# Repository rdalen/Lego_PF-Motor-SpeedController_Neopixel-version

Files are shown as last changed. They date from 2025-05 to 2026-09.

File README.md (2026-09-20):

# LEGO Power Function (PF) Motor speed controller

A DIY PWM speed controller for LEGO Power Functions motors, featuring a rotary encoder and 16-LED NeoPixel speed/direction indicator.
Inspired by the classic Lego train speed regulator (2868)




<p align="center"><i>2868 Lego train speed regulator</i></p>

---

## Features
- PWM control of LEGO Power Functions motors
- Forward and reverse operation
- Rotary encoder speed control
- 16-LED NeoPixel speed/direction indicator
- Adjustable NeoPixel brightness
- Push-button control
- Long-press reset to stop/default brightness
- Compatible with Arduino Pro Mini and LGT8F328P MiniEVB
- 9 Vdc power input
- Open hardware and software design

---

## Specifications

| Specification  | Value |
| --- | --- |
| Supply voltage | 9Vdc |
| Output voltage | PWM, 0 - 9V |
| Motor driver | DRV8833 |
| MCU | ATmega328P / LGT8F328P |
| NeoPixel ring  | 16 LEDs |
| Rotary encoder | EC11 |
| PCB size | 76 × 100 mm |
| PCB version | v1.1 |
| Motor outputs  | 1 |
| Control | Rotary encoder + push button |

---

## Description
It is based on an Arduino ProMini (or clone) and has a DRV8833 Motor driver module, a Rotary encoder and a 16 LED Neopixel Ring as forward/reverse speed indicator.
The conventional train regulator gives an analog 0-9V output signal. 
In this design, the PF motor is controlled with a Pulse Width Modulation (PWM) output signal. 
This means that the motor speed is controlled by varying the duty cycle of a square wave signal.

Earlier I made [another version](https://github.com/rdalen/Lego_PF-Motor-SpeedController) of a Lego speed controller based on the well known NE555 timer-IC. 

---

## Hardware

- 1× PCB
- 1× MCU Module Arduino Pro Mini or LGT8F328P MiniEVB
- 1× DRV8833 motor driver module
- 1× 16-LED NeoPixel ring
- 1× EC11 rotary encoder with push button
- LEGO PF connectors
- 4-core cable
- 9Vdc power supply / LEGO 8881 battery box
- enclosure material
- 3D-printed knob

Here is the PCB BOM list;



---

### MCU Module

For the MCU modules both the Arduino ProMini and the [LGT8F328P LQFP32 MiniEVB](https://wolles-elektronikkiste.de/en/minievb-boards-an-overview) (Pro Mini Style) can be used or even the [LGT8F328P SSOP20 MiniEVB](https://wolles-elektronikkiste.de/en/minievb-boards-an-overview) (pseudo Pro Mini Style).  

  

You can buy the LGT8F328P MiniEVB modules on AliExpress very cheap.  
I used the 5V version, because not all types of Neopixels are compatible with 3V3.  

---

## The Design
The [design](/docs/Lego%20PF%20Motor%20speed%20controller%20with%20Neopixel%20-%20Schematic.pdf) is made in KiCad 9.0 and is straight forward.  
It can be powered by, for example, a 9V Lego battery box (8881) or by an external 9Vdc power adapter.  
I first tested it in a breadboard setup. 



---

## Build overview

1. Order/assemble the PCB
2. Install the MCU and peripheral modules
3. Modify the PF Cable J11
4. Connect the PF input and motor output
5. Upload the firmware
6. Build the enclosure
7. Install the PCB, encoder and NeoPixel ring
8. Connect the 9Vdc supply
9. Test motor direction and speed indication

---

### The PCB
I designed a 76x100mm PCB, which I ordered from JLCPCB. 



The pcb design takes into account the footprint of the different MCU modules, however **only 1 of the MCU modules needs to be placed**.  

  

PCB v1.0 is shown in the photographs below. It has the issue described in [issue #1](https://github.com/rdalen/Lego_PF-Motor-SpeedController_Neopixel-version/issues/1).  
I still have a few v1.0 boards available for experimenting and sharing. The v1.0 PCB files are also available in the KiCad folder of this repository.

PCB [v1.1](https://github.com/rdalen/Lego_PF-Motor-SpeedController_Neopixel-version/blob/main/src/KiCad9.0/Lego%20PF-Motor%20PWM%20Speedcontroller%20-%20Neopixel%20version-v1.1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) fixes this issue and is the recommended version for new builds.

---

### The DIY PF Cable

On AliExpress you can buy PF connectors and 4 core wire and make your own Lego PF connection cables.
Before assembling the Input PF cable (connected to J11 in the schematic), I removed the C1 and C2 contacts from the Bottom part of the connector so that this connector can be used to connect both the battery box (via the 0V and 9V contacts in the BOTTOM part) as the Lego PF-motor as well (via the C1 and C2 contacts in the TOP part). 

  

The output PF cable (connected to J13 in the schematic) is not modified (so has all its contacts).
So the PF-motor can be connected or to the input connector (connected to the Battery box) or to the output connector.  

See [this article](https://www.philohome.com/pf/pf.htm) about the working of the LEGO Power Function cable.

---

### The Programming

To upload the sketch from your computer into the Arduino board you will need a FTDI USB to TTL Adapter.  



Then;  
- Install the following libraries:
  - [lgt8fx library](https://github.com/dbuezas/lgt8fx?tab=readme-ov-file) (When you use a LGT8F328P MiniEVB Board)
  - [NeoPixel library](https://github.com/adafruit/Adafruit_NeoPixel)
  - [Rotary library](https://github.com/buxtronix/arduino/tree/master/libraries/Rotary)
- Download the sketch (You can also download the sketch from my github)
- Set the proper board settings (see picture below for the LGT8F328P board settings) and upload the sketch



For clarification;
- The NeoPixel ring indicates the output signal (similar to the big yellow button on the conventional LEGO train speed regulator).  
- Turning the Rotary encoder knob to the right will increase the speed in forward direction (Green color), turning to the left will decrease the speed to 0 (LED8 is the center of the indication scale) and then increases the speed in reverse direction (Red color).  
- NeoPixel LED0 is set to blue as power-on indication. 
- When your Rotary encoder is equipped with a push button; a short button press will increase the brightness of the LEDs (in 9 steps) and a long button press (>2sec) will reset the brightness to the default 10% and set the speed to 0 (Stop).

---

### Yellow knob

I designed a big 45mm knob in FreeCAD (v1.0) for the Rotary encoder and 3d-printed it in yellow  
The design is parametric, so the knob dimensions can be modified in the spreadsheet tab 

  

---

### Enclosure

The enclosure is a clever laser-cut design from [this](https://boxes.hackerspace-bamberg.de/?language=en) site with lots of boxes. It is based on [this console](https://boxes.hackerspace-bamberg.de/Console2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) and has a [small box](https://boxes.hackerspace-bamberg.de/ABox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) on the back for the Battery box.  
Then I imported the SVG output files into the lasercutter software (XTool) and made cutouts for the NeoPixel ring LEDs and the other things. The labels on the parts come on the inside of the box.   

  

The holes in the front panel for the NeoPixel ring LEDs were reworked with a dremel tool to mill out the screws and SMD resistors.  

  

---

### Assembly

  

  

  

  

  

  

Watch the video's  

Watch the video (https://youtube.com/shorts/yDlcr6ofd3M)

---

## The Result
And this is what it looks like when assembled

  

Watch the video's  

Watch the video (https://youtube.com/shorts/p-FWXSREwLY)  

Watch the video (https://youtube.com/shorts/qJE7di6izpw)   

---

## DIY Guide
For a guide on how to build this project, check out the tutorial at [Instructables](https://www.instructables.com/Lego-Power-Function-PF-Motor-Speed-Controller-With/).

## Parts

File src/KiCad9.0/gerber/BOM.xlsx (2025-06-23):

Designator | Quantity | Value
C1, C4 | 2 | 100uF
C2, C3, C5, C6 | 4 | 100n
D1 | 1 | 1N5822
D2 | 1 | NeopixelRing-16LEDs
J1 | 1 | HeaderPin 01x04
J2 | 1 | HeaderPin 01x02
J3 | 1 | HeaderSocket 01x04
R1 | 1 | 470R
U1 | 1 | OR; LGT8F328P LQFP32 MiniEVB - ProMini board 5V OR; Arduino ProMini board 5V
U2 | 1 | OR; LGT8F328P SSOP20 MiniEVB - pseudo ProMini board 5V
U3 | 1 | DRV8833 Motor Driver Board
U4 | 1 | Rotary Encoder EC11

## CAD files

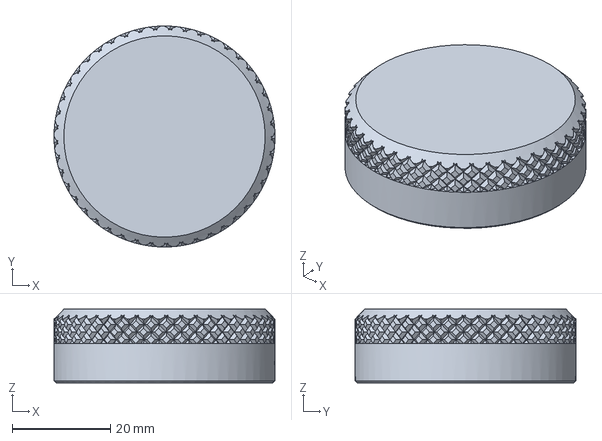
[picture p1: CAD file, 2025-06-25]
src/FreeCad/Knob_knurled - parametric_45mm.FCStd
45.0 x 45.0 x 15.0 mm

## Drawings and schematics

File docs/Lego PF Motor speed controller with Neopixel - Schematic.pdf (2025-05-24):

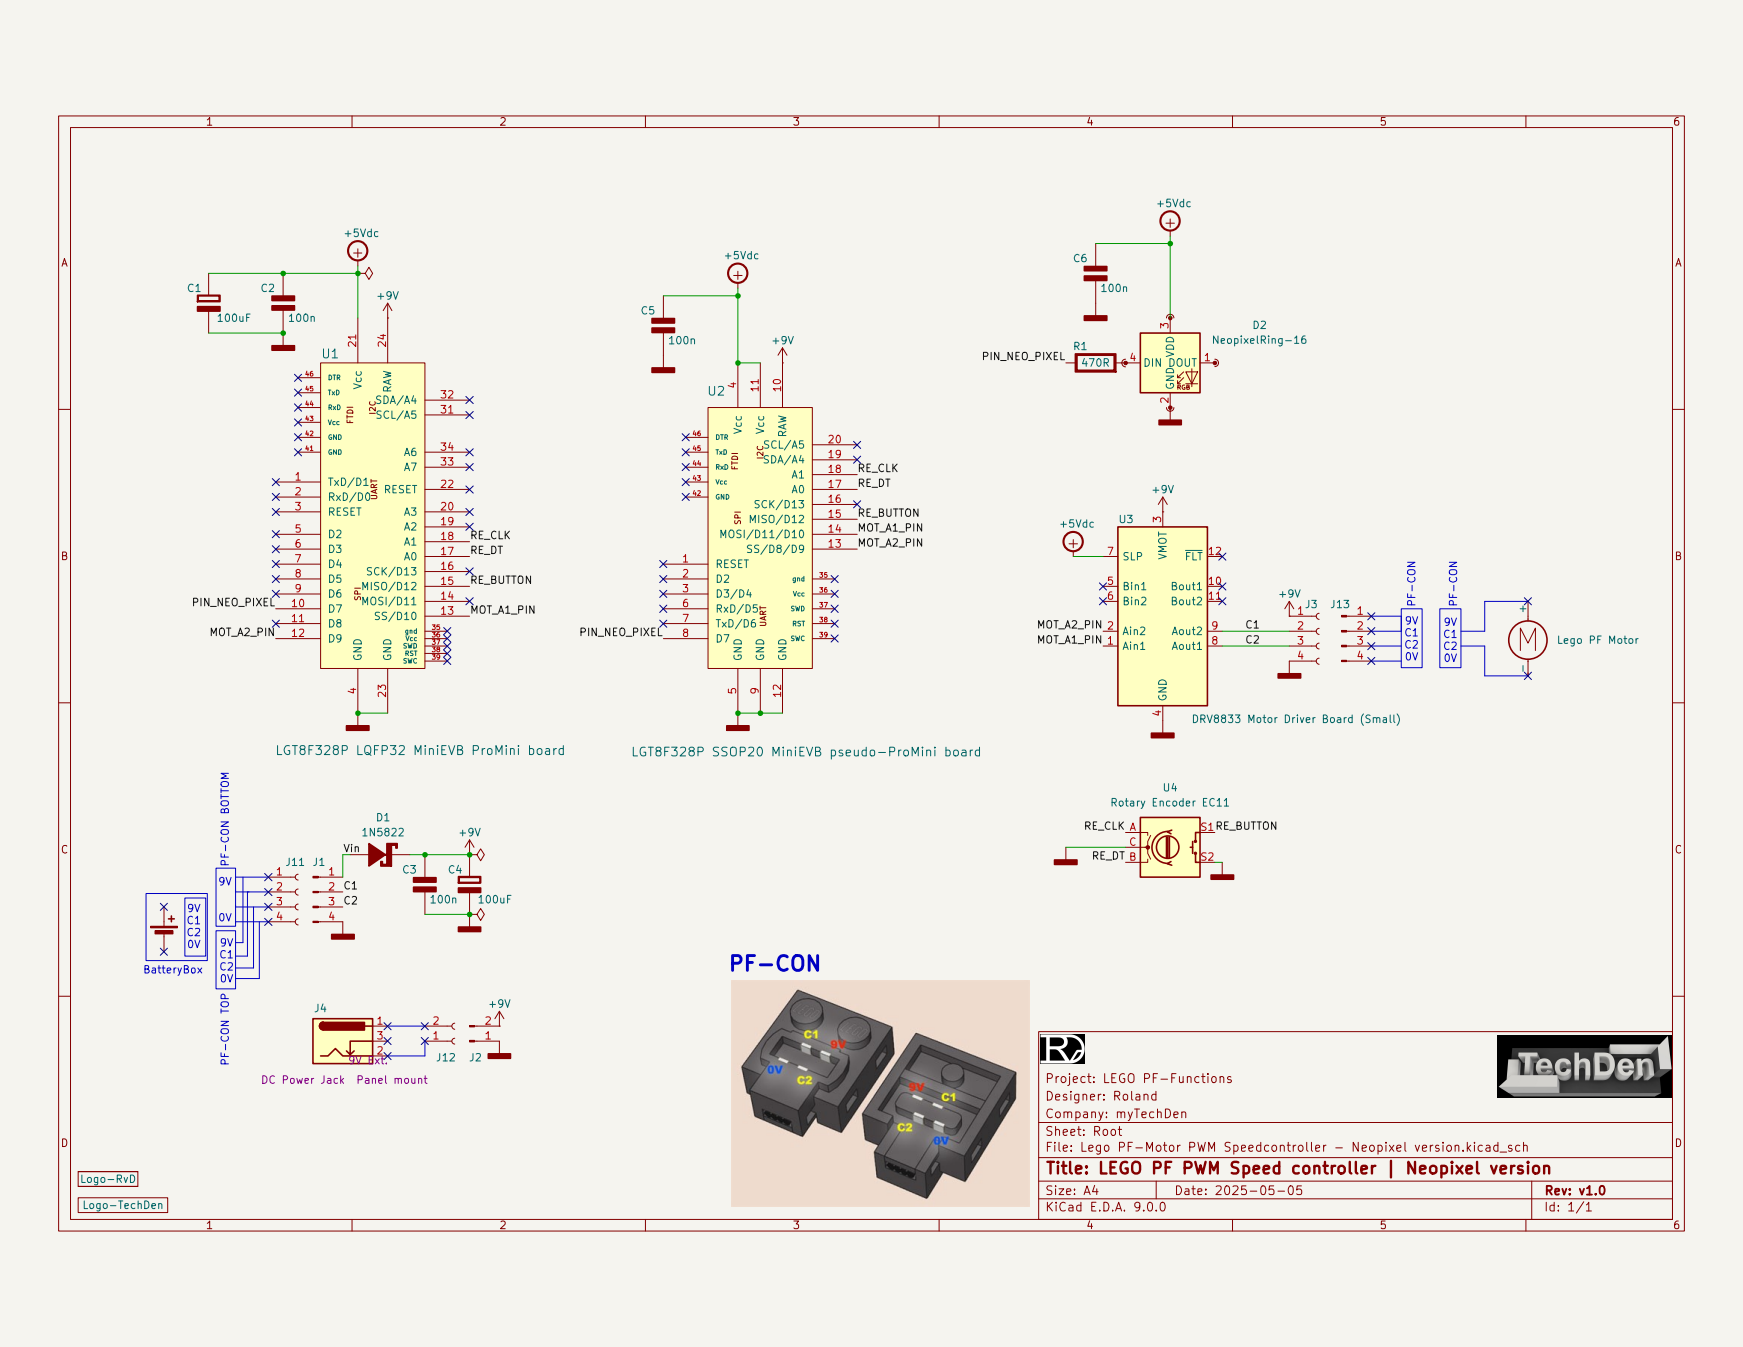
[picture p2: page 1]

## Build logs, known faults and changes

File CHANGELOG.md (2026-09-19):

## [1.1] - 2026-09-19

### Improved

* Updated and expanded the README documentation.
* Added project features, specifications, hardware list, and build overview.
* Clarified the differences between PCB v1.0 and v1.1.
* Documented PCB v1.1 as the recommended version for new builds.
* Improved wording, terminology, and general readability.

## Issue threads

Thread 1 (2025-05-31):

Please update the footprint of the Neopixel Ring-16LEDs

rdalen, 2025-05-31:
##Wrong mounting hole dimensions
The Mounting holes of the Neopixel Ring-16LEDs in v1.0 PCB are at X54.61 x Y36.83mm, this must become X53 x Y36mm.
And some type of Neopixel-16LEDs  rings has the mounting holes at X35 x Y58

Hereby the request to adjust the footprint on both types of Neopixel Ring 16LEDs

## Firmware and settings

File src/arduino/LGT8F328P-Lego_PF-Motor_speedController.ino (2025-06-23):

/* This sketch controls two DC Motors with DRV8833 Motor Driver for the 32MHz LGT8F328P chip (ATMEGA328P upgrade) 
 * The PWM pins of the 328-SSOP20 (pseudo Pro mini) are
 * D3,D5 (also RxD - so no serial monitor possible), D6 (also TxD), D9, D10/D11, 
 *
 * To select the boards:
 * 1 - select LGTF328 board
 * 2 - select the variant 328-LQFP32 for the nano or the Pro mini stype
       or 328-SSOP20 for the pseudo Pro mini style

 * 3 - select the clock source Internal 32MHz
 * 4 - Select the clock divider factor; 2 (16Mhz clock because of the NeoPixel library
 * 5 - select the port
 * 
 * See https://wolles-elektronikkiste.de/en/minievb-boards-an-overview
 * and https://github.com/dbuezas/lgt8fx?tab=readme-ov-file
 * 
 * Rotary.h; https://github.com/buxtronix/arduino/tree/master/libraries/Rotary
 */

#include <Adafruit_NeoPixel.h>
#include <Rotary.h>  //this library solves the bounching issue with a state machine

#define RE_DT 14  // Rotary encoder signal DT (output A)
#define RE_CLK 15  // Rotary encoder signal CLK (output B)
#define RE_BUTTON 12 // for possible Rotary encoder button | active LOW
#define RE_MAX HALFSCALE // Count value of the half rotation of the Rotary encoder - will be scaled to a PWM value from 0-255
#define PWM_MAX 255

//Change OUTPUTA and OUTPUTB to change the RotaryEncoder direction
#define OUTPUTB RE_CLK //... also known as
#define OUTPUTA RE_DT

#define LONGPRESSTIME 2000 // for possible Rotary encoder button

//Rotery encoder instantiation
// The Rotary encoder is wired with the common to ground and the two outputs to pins OUTPUTA and OUTPUTB.
Rotary rotary = Rotary(OUTPUTA, OUTPUTB);

// Define the control inputs | Hence; the PWM pins of the arduino Uno/Nano/mini are; 3, 5, 6, 9, 10, 11
// SLEEP pin must be pulled HIGH
#define MOT_A1_PIN 10
#define MOT_A2_PIN 9

#define PIN_NEO_PIXEL 7  // Arduino pin that connects to NeoPixel ring
#define NUM_PIXELS 16 // The number of LEDs (pixels) on NeoPixel ring
#define HALFSCALE NUM_PIXELS/2 //Half scale of the Neopixel ring (is stop)
#define BRIGHTNESS 25 //default on scale 0-255
#define BRIGHNESS_STEP 25
#define COLORGREEN 0,255,0
#define COLORRED 255,0,0
#define COLORBLUE 0,0,255

Adafruit_NeoPixel NeoPixel(NUM_PIXELS, PIN_NEO_PIXEL, NEO_GRB + NEO_KHZ800); // set the NeoPixel ring initialization

int RE_counter = 0; // Rotary encoder counter
int valuePMW; // PWM value
int valuePMWlast = 0; 
bool buttonREActive;
bool longPressREActive;
long buttonRETimer;
int neoBrightness = BRIGHTNESS;

void setup() {

  // Initialize the serial UART
  Serial.begin(115200);
  Serial.println("start sketch");

  NeoPixel.begin();  // initialize the NeoPixel strip object
  NeoPixel.clear(); NeoPixel.show(); // reset all pixels  
  delay(500);
  NeoPixel.setPixelColor(0, NeoPixel.Color(COLORBLUE));  // set pixel 0 to blue as power on indication
  NeoPixel.setBrightness(BRIGHTNESS);  
  NeoPixel.show(); // show all the set pixels on neopixel ring
 
  Serial.print("Number of Pixels "); Serial.println(NUM_PIXELS);
  Serial.print("Half scale "); Serial.println(HALFSCALE);
  
  // Set the Rotary Encoder pins to INPUT
  pinMode(RE_BUTTON, INPUT_PULLUP);  //for possible Rotary encoder button | active LOW
//  pinMode (OUTPUTA,INPUT_PULLUP); // Rotary encoder OUTPUTA signal
//  pinMode (OUTPUTB,INPUT_PULLUP); // Rotary encoder OUTPUTB signal

  // Set all the motor control pins to OUTPUT
  pinMode(MOT_A1_PIN, OUTPUT);
  pinMode(MOT_A2_PIN, OUTPUT);
//  pinMode(MOT_B1_PIN, OUTPUT);
//  pinMode(MOT_B2_PIN, OUTPUT);

  // Turn off motors - Initial state
  digitalWrite(MOT_A1_PIN, LOW);
  digitalWrite(MOT_A2_PIN, LOW);
//  digitalWrite(MOT_B1_PIN, LOW);
//  digitalWrite(MOT_B2_PIN, LOW);

}

void loop() {

  valuePMW = map(read_RE(), 0, RE_MAX, 0, PWM_MAX) ; // map Rotary Encoder value to 255 steps (PWM)
  if (valuePMW != valuePMWlast) {
    Serial.print("PWM "); Serial.println(valuePMW);
    valuePMWlast = valuePMW;
    set_motor_pwm(valuePMW, MOT_A1_PIN, MOT_A2_PIN); //set PWM Motor output
    setNeopixels(valuePMW); //set value in neopixel ring
  }

  // for possible Rotary encoder button
  if (digitalRead(RE_BUTTON) == LOW) {  // Button pressed
   if (buttonREActive == false) {
     buttonREActive = true;
     buttonRETimer = millis();
   }
   if ((millis() - buttonRETimer > LONGPRESSTIME) && (longPressREActive == false)) {
     longPressREActive = true;
     Serial.println("buttonRE LongPressed"); 
//     valuePMW=0;
//     set_motor_pwm(valuePMW, MOT_A1_PIN, MOT_A2_PIN); //set PWM Motor output
     RE_counter=0;
     neoBrightness = BRIGHTNESS; //set default
     NeoPixel.setBrightness(neoBrightness);  
     NeoPixel.show(); // show all the set pixels on neopixel ring
   }
  } 
  else {                            // buttonRE released
    if (buttonREActive == true) {
      if (longPressREActive == true) {
        longPressREActive = false;
      } else {
        Serial.println("buttonRE ShortPressed");
        //on button press increase brightness in 10 steps
        neoBrightness = neoBrightness + BRIGHNESS_STEP;
        if (neoBrightness>255) {neoBrightness = BRIGHTNESS;}
        NeoPixel.setBrightness(neoBrightness);  
        NeoPixel.show(); // show all the set pixels on neopixel ring
        Serial.print("Brightness: "); Serial.println(neoBrightness);
         
      }
      buttonREActive = false;
    }
  }

}

//Read Rotary encoder
int read_RE() { 
  unsigned char result = rotary.process();
  if (result == DIR_CW) { //if turn Rotery encoder clockwise
    RE_counter++;
    if (RE_counter > RE_MAX) RE_counter=RE_MAX;
    Serial.print("Rotary Encoder: "); Serial.println(RE_counter);
  } else if (result == DIR_CCW) { //if turn Rotery encoder counter clockwise
    RE_counter--;
    if (RE_counter < -RE_MAX) RE_counter=-RE_MAX;
    Serial.print("Rotary Encoder: "); Serial.println(RE_counter);
  }
  return(RE_counter);
}

//PWM Motor output
void set_motor_pwm(int pwm, int IN1_PIN, int IN2_PIN)
{
  if (pwm < 0) {  // if reverse
    analogWrite(IN1_PIN, -pwm);
    digitalWrite(IN2_PIN, LOW);

  } else { // else stop or forward
    digitalWrite(IN1_PIN, LOW);
    analogWrite(IN2_PIN, pwm);
  }
//  Serial.print("Motor - PWM: "); Serial.println(pwm);
}

//Set neopixel ring to value - halfscale is stop
void setNeopixels(int pwm)
{
//  Serial.print("Neo - PWM: "); Serial.println(pwm);  
  NeoPixel.clear(); //Reset all pix
  if (pwm < 0) {  // if reverse
    for (int pixel = 0; pixel < HALFSCALE; pixel++) {  // for each pixel on the left halfscale
//      Serial.print("Neo - pixel reverse: "); Serial.print(HALFSCALE-pixel); Serial.print(" "); Serial.println(pixel * (PWM_MAX / (HALFSCALE-1)));  
      if (((pixel) * (PWM_MAX / (HALFSCALE-1))) < -valuePMW) { // fill pixels based on the rotary encoder value
        NeoPixel.setPixelColor(HALFSCALE-pixel, NeoPixel.Color(COLORRED));  // set these pixels to red color
      }
    }
  }
  if (pwm > 0) { // forward
    for (int pixel = HALFSCALE; pixel < NUM_PIXELS; pixel++) {  // for each pixel on the right halfscale
//      Serial.print("Neo - pixel reverse: "); Serial.print(pixel); Serial.print(" "); Serial.println((pixel - HALFSCALE) * (PWM_MAX / (HALFSCALE - 1)));  
      if (((pixel - HALFSCALE) * (PWM_MAX / (HALFSCALE - 1))) < valuePMW) { // fill pixels based on the rotary encoder value
        NeoPixel.setPixelColor(pixel, NeoPixel.Color(COLORGREEN));  // set these pixels to green color
      }
    }
  }
//  if (pwm!=0) {NeoPixel.setPixelColor(0, NeoPixel.Color(COLORBLUE));}  // set pixel 0 to Blue color
  NeoPixel.setPixelColor(0, NeoPixel.Color(COLORBLUE));  // set pixel 0 to blue as power on indication
  NeoPixel.setBrightness(neoBrightness);  
  NeoPixel.show(); // show all the set pixels on neopixel ring

}

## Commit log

2025-05-24 Rename Lego PF Motor speed controller with Neopixel - Schematic.pdf to docs/Lego PF Motor speed controller with Neopixel - Schematic.pdf
2025-05-24 Update and rename LGT8F328P-Lego_PF-Motor_speedController.ino to src/arduinocode/LGT8F328P-Lego_PF-Motor_speedController.ino
2025-05-24 Update and rename src/arduinocode/LGT8F328P-Lego_PF-Motor_speedController.ino to src/LGT8F328P-Lego_PF-Motor_speedController.ino
2025-05-24 Update and rename src/LGT8F328P-Lego_PF-Motor_speedController.ino to src/arduino/LGT8F328P-Lego_PF-Motor_speedController.ino
2025-05-31 fixed #1
    footprint modified on 2 types of Neopixel Ring 16LEDs
2025-06-25 Rename src/Knob_knurled - parametric_45mm.FCStd to src/FreeCad/Knob_knurled - parametric_45mm.FCStd
    [Knob_knurled - parametric_45mm.FCStd]
2025-06-27 Rename Lego PF Motor speed controller-neopixel - Lasercuts parts1.svg to Lego PF Motor speed controller-neopixel - Lasercuts parts1.svg
2025-06-27 Rename src/Lego PF Motor speed controller-neopixel - Lasercuts parts1.svg to src/Lasercut_files/Lego PF Motor speed controller-neopixel - Lasercuts parts1.svg
